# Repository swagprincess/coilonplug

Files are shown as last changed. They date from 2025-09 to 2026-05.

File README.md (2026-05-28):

# Dwell converter board

This board lets you use a Toyota/Audi/etc "coil on plug" ignition system with the stock ecu in a Mazda MX5/Miata (1989-2005).

The board will take in a variable dwell signal for the stock coilpack and output a (falling edge synchronised) stable, adjustable dwell pulse.

Current setting is 70 "ticks" of TIMER1, around 2.2ms, correct for Toyota COP's at running voltages (should be good for Audi R8 coils too).

Written in C for an AtTiny84A.

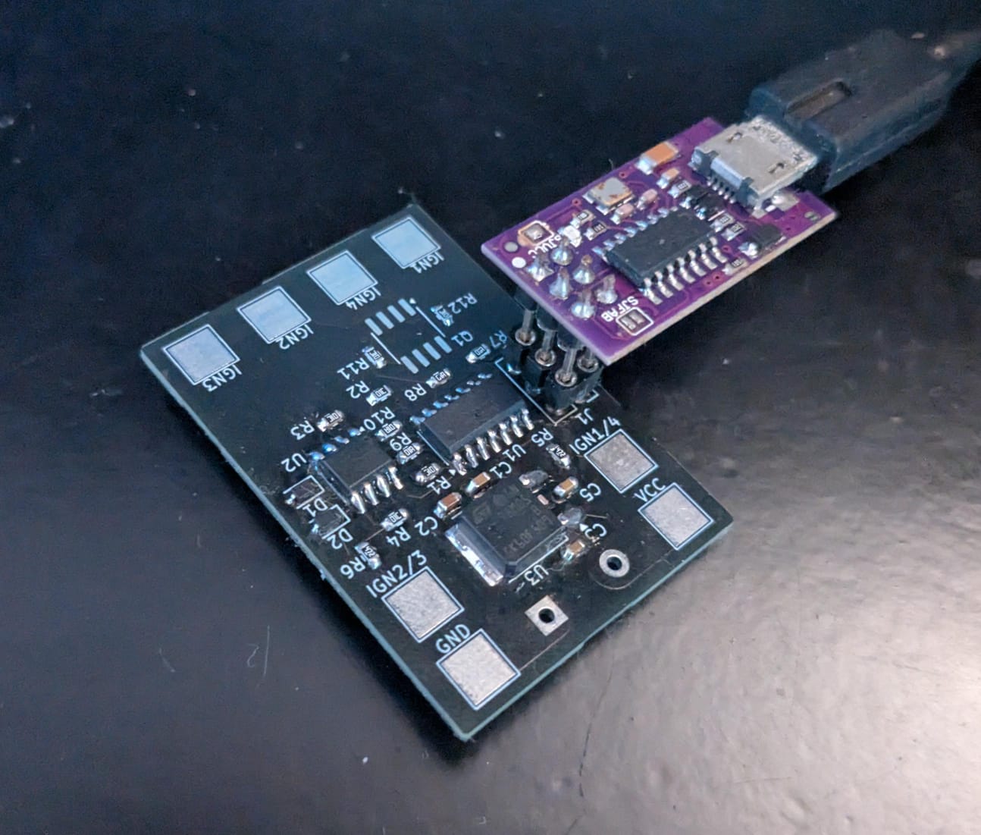
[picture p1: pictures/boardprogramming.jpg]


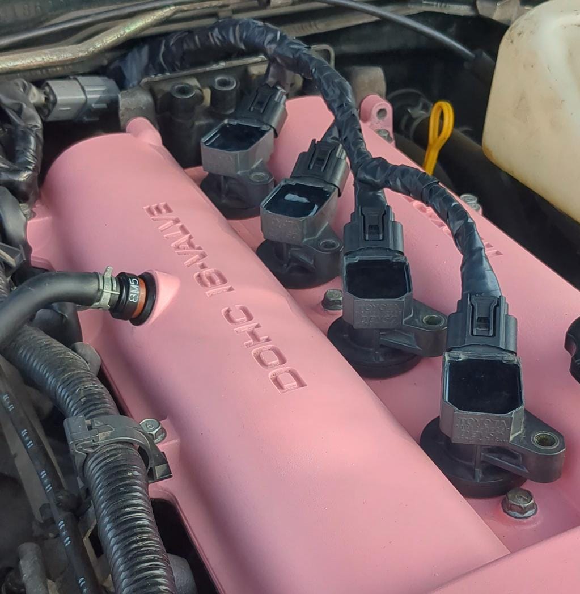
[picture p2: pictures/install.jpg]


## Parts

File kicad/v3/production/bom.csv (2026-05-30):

Designator | Footprint | Quantity | Value | LCSC Part #
C1, C3 | 0603 | 2 | 100n | C77055
C2 | 0603 | 1 | 330n | C354382
C4 | 0603 | 1 | 10u | C2959727
D1, D2 | D_SOD-323F | 2 | MM3Zxx | C154578
Q1 | SOIC-8_3.9x4.9mm_P1.27mm | 1 | DMP3098LSD-13 | C531177
R1, R2, R3, R4 | 0603 | 4 | 10k | C116677
U1 | SOIC-14_3.9x8.7mm_P1.27mm | 1 | ATtiny84A-SS | C1340034
U2, U3 | SOT-23-5 | 2 | SN74LVC1G17DBVR | C7836
U4 | SOT-89-3 | 1 | L78L05_SOT89 | C42738

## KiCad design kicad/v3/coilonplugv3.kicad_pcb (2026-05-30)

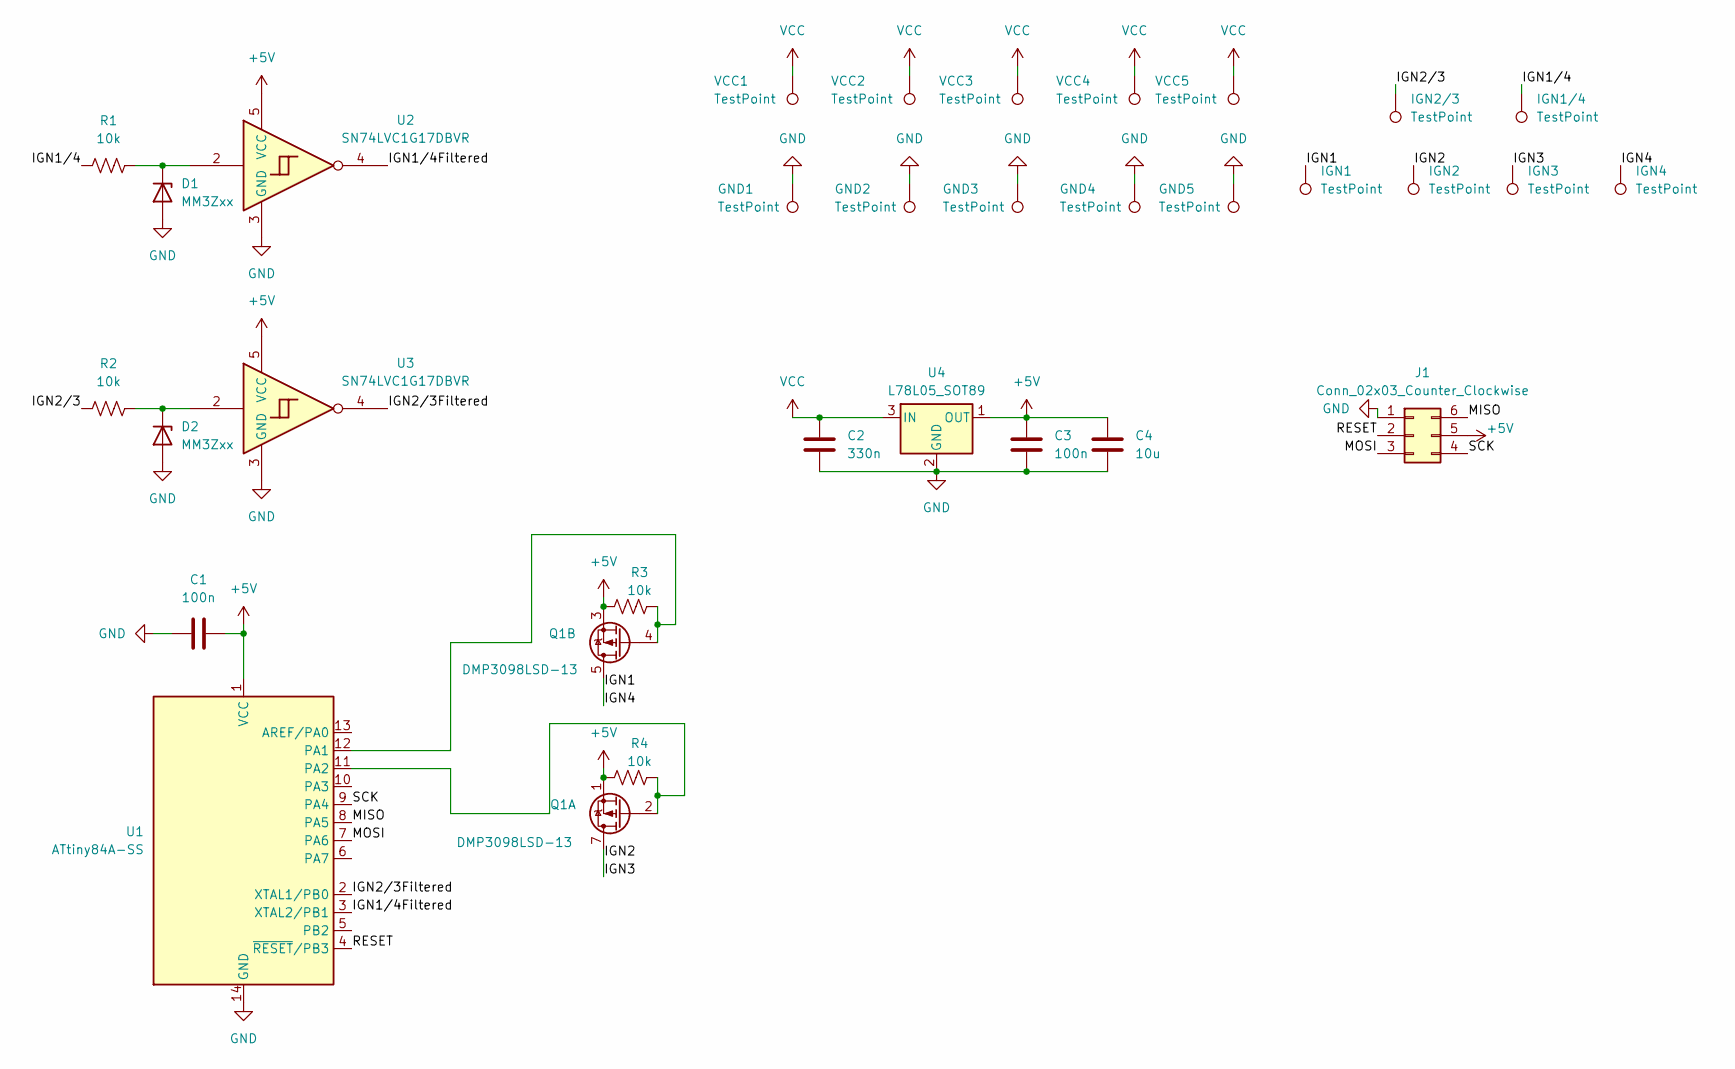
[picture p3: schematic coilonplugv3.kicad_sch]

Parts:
C1, C3: 100n; C_0603_1608Metric; LCSC Part # C77055
C2: 330n; C_0603_1608Metric; LCSC Part # C354382
C4: 10u; C_0603_1608Metric; LCSC Part # C2959727
D1, D2: MM3Zxx; D_SOD-323F; LCSC Part # C154578
GND1, GND2, GND3, GND4, GND5: TestPoint; TestPoint_Pad_2.5x2.5mm
IGN1, IGN1/4, IGN2, IGN2/3, IGN3, IGN4: TestPoint; TestPoint_Pad_2.5x2.5mm
J1: Conn_02x03_Counter_Clockwise; PinHeader_2x03_P2.54mm_Vertical; LCSC Part # C2764576
Q1: DMP3098LSD-13; SOIC-8_3.9x4.9mm_P1.27mm; LCSC Part # C531177
R1, R2, R3, R4: 10k; R_0603_1608Metric; LCSC Part # C116677
U1: ATtiny84A-SS; SOIC-14_3.9x8.7mm_P1.27mm; LCSC Part # C1340034
U2, U3: SN74LVC1G17DBVR; SOT-23-5; LCSC Part # C7836
U4: L78L05_SOT89; SOT-89-3; LCSC Part # C42738
VCC1, VCC2, VCC3, VCC4, VCC5: TestPoint; TestPoint_Pad_2.5x2.5mm

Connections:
+5V: C1.1, C3.1, C4.1, J1.5, Q1.1 (S1), Q1.3 (S2), R3.2, R4.2, U1.1 (VCC), U2.5 (VCC), U3.5 (VCC), U4.1 (OUT)
/IGN1: IGN1.1 (1_1), IGN4.1 (1_1), Q1.5 (D2), Q1.6 (D2)
/IGN1/4: IGN1/4.1 (1_1), R1.1
/IGN1/4Filtered: U1.3 (XTAL2/PB1), U2.4
/IGN2: IGN2.1 (1_1), IGN3.1 (1_1), Q1.7 (D1), Q1.8 (D1)
/IGN2/3: IGN2/3.1 (1_1), R2.1
/IGN2/3Filtered: U1.2 (XTAL1/PB0), U3.4
/MISO: J1.6, U1.8 (PA5)
/MOSI: J1.3, U1.7 (PA6)
/RESET: J1.2, U1.4 (~RESET/PB3)
/SCK: J1.4, U1.9 (PA4)
GND: C1.2, C2.2, C3.2, C4.2, D1.2 (A), D2.2 (A), GND1.1 (1_1), GND2.1 (1_1), GND3.1 (1_1), GND4.1 (1_1), GND5.1 (1_1), J1.1, U1.14 (GND), U2.3 (GND), U3.3 (GND), U4.2 (GND)
unnamed: D1.1 (K), R1.2, U2.2
unnamed: D2.1 (K), R2.2, U3.2
unnamed: Q1.2 (G1), R4.1, U1.11 (PA2)
unnamed: Q1.4 (G2), R3.1, U1.12 (PA1)
VCC: C2.1, U4.3 (IN), VCC1.1 (1_1), VCC2.1 (1_1), VCC3.1 (1_1), VCC4.1 (1_1), VCC5.1 (1_1)

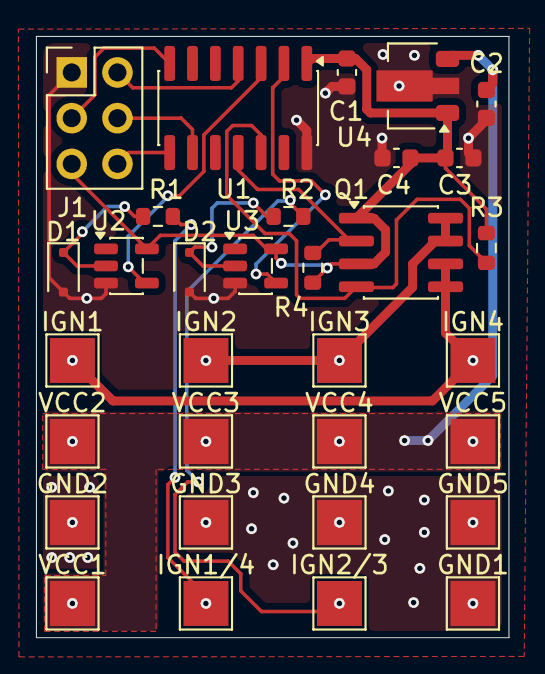
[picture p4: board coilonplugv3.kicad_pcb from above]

Board: 2 copper layers, 26.2 x 33.4 mm, 32 parts (0 on the bottom side), 17 nets.

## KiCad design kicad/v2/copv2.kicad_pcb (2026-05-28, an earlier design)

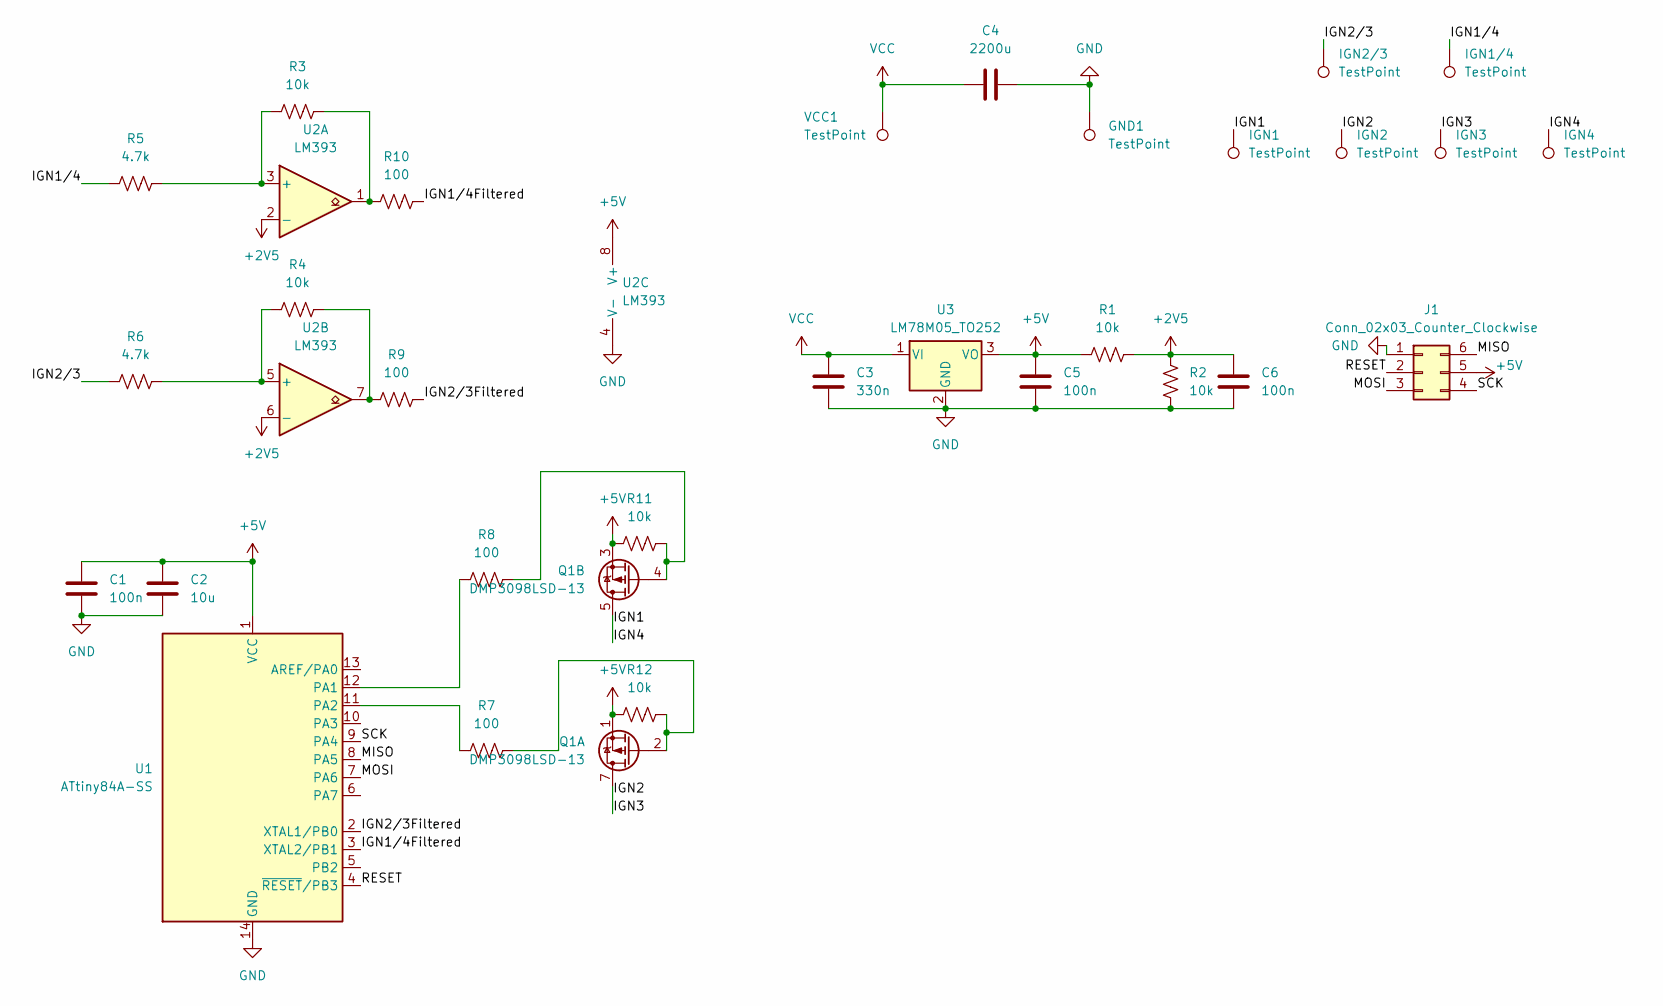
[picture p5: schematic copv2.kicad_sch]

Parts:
C1, C5, C6: 100n; C_0603_1608Metric; LCSC Part # C77055
C2: 10u; C_0603_1608Metric; LCSC Part # C2959727
C3: 330n; C_0603_1608Metric; LCSC Part # C107070
C4: 2200u; CP_Radial_D12.5mm_P5.00mm; LCSC Part # C111500
GND1: TestPoint; TestPoint_Pad_4.0x4.0mm
IGN1, IGN1/4, IGN2, IGN2/3, IGN3, IGN4: TestPoint; TestPoint_Pad_4.0x4.0mm
J1: Conn_02x03_Counter_Clockwise; PinHeader_2x03_P2.54mm_Vertical; LCSC Part # C2764576
Q1: DMP3098LSD-13; SOIC-8_3.9x4.9mm_P1.27mm; LCSC Part # C531177
R1, R2, R3, R4, R11, R12: 10k; R_0603_1608Metric; LCSC Part # C98220
R5, R6: 4.7k; R_0603_1608Metric; LCSC Part # C116697
R7, R8, R9, R10: 100; R_0603_1608Metric; LCSC Part # C105588
U1: ATtiny84A-SS; SOIC-14_3.9x8.7mm_P1.27mm; LCSC Part # C1340034
U2: LM393; SOIC-8_3.9x4.9mm_P1.27mm; LCSC Part # C32901
U3: LM78M05_TO252; TO-252-2; LCSC Part # C58069
VCC1: TestPoint; TestPoint_Pad_4.0x4.0mm

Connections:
+2V5: C6.1, R1.2, R2.2, U2.2 (-), U2.6 (-)
+5V: C1.1, C2.1, C5.1, J1.5, Q1.1 (S1), Q1.3 (S2), R1.1, R11.2, R12.2, U1.1 (VCC), U2.8 (V+), U3.3 (VO)
/IGN1: IGN1.1, IGN4.1, Q1.5 (D2), Q1.6 (D2)
/IGN1/4: IGN1/4.1, R5.1
/IGN1/4Filtered: R10.1, U1.3 (XTAL2/PB1)
/IGN2: IGN2.1, IGN3.1, Q1.7 (D1), Q1.8 (D1)
/IGN2/3: IGN2/3.1, R6.1
/IGN2/3Filtered: R9.1, U1.2 (XTAL1/PB0)
/MISO: J1.6, U1.8 (PA5)
/MOSI: J1.3, U1.7 (PA6)
/RESET: J1.2, U1.4 (~RESET/PB3)
/SCK: J1.4, U1.9 (PA4)
GND: C1.2, C2.2, C3.2, C4.1, C5.2, C6.2, GND1.1, J1.1, R2.1, U1.14 (GND), U2.4 (V-), U3.2 (GND); also elsewhere on the board
unnamed: Q1.2 (G1), R7.2, R12.1
unnamed: Q1.4 (G2), R8.1, R11.1
unnamed: R4.2, R9.2, U2.7
unnamed: R3.2, R10.2, U2.1
unnamed: R8.2, U1.12 (PA1)
unnamed: R7.1, U1.11 (PA2)
unnamed: R3.1, R5.2, U2.3 (+)
unnamed: R4.1, R6.2, U2.5 (+)
VCC: C3.1, C4.2, U3.1 (VI), VCC1.1; also elsewhere on the board

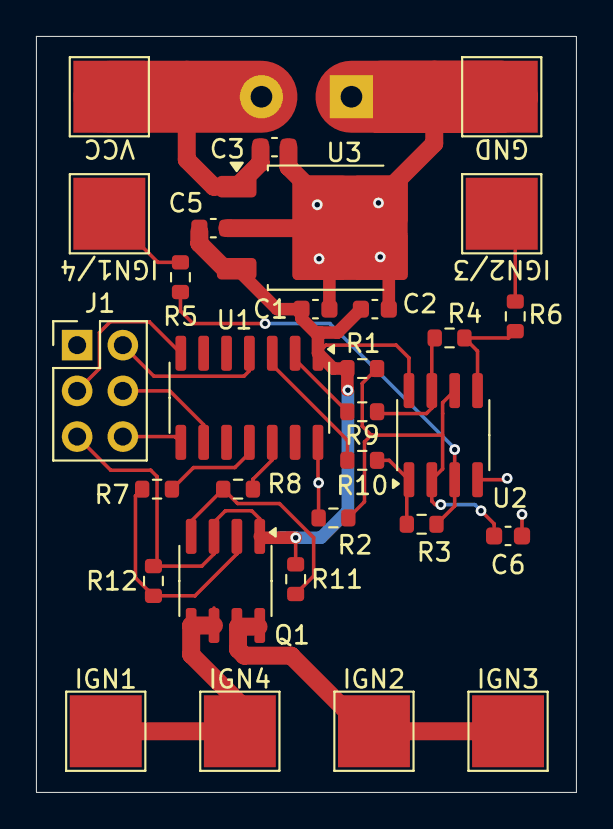
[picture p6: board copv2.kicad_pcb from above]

Board: 2 copper layers, 30.0 x 42.0 mm, 31 parts (1 on the bottom side), 22 nets.

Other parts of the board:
GND: TestPoint; TestPoint_Pad_4.0x4.0mm
VCC: TestPoint; TestPoint_Pad_4.0x4.0mm

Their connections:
GND: GND.1; also elsewhere on the board
VCC: VCC.1; also elsewhere on the board

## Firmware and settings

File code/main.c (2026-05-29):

#define F_CPU 8000000UL

#include <avr/io.h>
#include <util/delay.h>
#include <avr/interrupt.h>
#include <stdint.h>
#include <stdlib.h>

#define true 1
#define false 0

volatile uint16_t delayBeforeLow = 0;  // passthrough test //ticks at 8mhz prescaler 256, assume 5ms base pulse and 3.5ms ish for first pulse
volatile uint16_t startTime14 = 0;
volatile uint16_t startTime23 = 0;
volatile uint16_t timeToGoLow23 = 0;
volatile uint16_t timeToGoLow14 = 0;
volatile uint8_t pulses = 0;
volatile uint8_t lastState23 = false;
volatile uint8_t lastState14 = false;
volatile uint8_t set23Low = false;
volatile uint8_t set14Low = false;


ISR(PCINT1_vect){ // interrupt for all port b pins

    uint8_t pins = PINB;

    if (!(pins & (1 << PB1)) && lastState14){    //IGN 1 & 4
        // PB1 is LOW, turn off PA2 (1 & 4)
        PORTA |= (1 << PA1); // set high for off

        delayBeforeLow = (uint16_t)(TCNT1 - startTime14) - 70; //2.2ms
        if (pulses <= 30){
            delayBeforeLow = (uint16_t)(TCNT1 - startTime14) - 110; // 3.5ms for startup first 30 igniton events
            pulses = pulses + 1;
        }

        lastState14 = false;
    }

    
    if (!(pins & (1 << PB0)) && lastState23){    //IGN 2 & 3
        // PB0 is LOW, turn off PA1 (2 & 3)
        PORTA |= (1 << PA2); // set high for off

        delayBeforeLow = (uint16_t)(TCNT1 - startTime23) - 70; //2.2ms
        if (pulses <= 30){
            delayBeforeLow = (uint16_t)(TCNT1 - startTime23) - 110; // 3.5ms for startup first 30 igniton events
            pulses = pulses + 1;
        }

        lastState23 = false;
    }


    if ((pins & (1 << PB1)) && !lastState14) {   //IGN 1 & 4
        // PB1 is HIGH
        startTime14 = (uint16_t)TCNT1; // set timer timestamp

        if (delayBeforeLow < 1){
            delayBeforeLow = 0;
        }

        timeToGoLow14 = (uint16_t)(startTime14 + delayBeforeLow);

        set14Low = true; // mark pin as has to go low eventually 

        lastState14 = true;
    }

 
    if ((pins & (1 << PB0)) && !lastState23) {   //IGN 2 & 3
        // PB0 is HIGH
        startTime23 = (uint16_t)TCNT1; // set timer timestamp

        if (delayBeforeLow < 1){
            delayBeforeLow = 0;
        }

        timeToGoLow23 = (uint16_t)(startTime23 + delayBeforeLow);

        set23Low = true; // mark pin as has to go low eventually 
        
        lastState23 = true;
    }
     
}


int main(void) {

    //set output pins as output and set high
    DDRA |= ((1 << DDA1) | (1<< DDA2));
    PORTA |= ((1 << PA1) | (1 << PA2));

    //set input pins as input
    DDRB &= ~((1 << DDB0) | (1 << DDB1));

    TCCR1B = 0; // stop timer

    TCCR1B |= (1 << CS12); // start timer at prescaler 256

    GIMSK |= (1 << PCIE1); //enable group 1 pin interrupts
    PCMSK1 |= (1 << PCINT8) | (1 << PCINT9); // allow pins to trigger interrupt

    sei(); //enable interrupts


    while (1){
        if (set23Low){
            cli(); //16 bit math and time sensitive stuff
            if ((uint16_t)TCNT1 >= timeToGoLow23){
                PORTA &= ~(1 << PA2); // set low to start trigger
                set23Low = false;
            }
            sei(); //enable interrupts
        }
        if (set14Low){
            cli(); //16 bit math and time sensitive stuff 
            if ((uint16_t)TCNT1 >= timeToGoLow14){
                PORTA &= ~(1 << PA1); // set low to start trigger
                set14Low = false;
            }
            sei(); //enable interrupts
        }
    }

}

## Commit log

2025-08-10 fix bunch of bs lol
    [main.c]
2025-08-10 fix bug with negative delays
    [main.c]
2025-08-11 fix base pulse delay
    [main.c]
2025-08-11 kicad added
    [bom.csv, copv2.kicad_pcb, copv2.kicad_sch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]
2025-08-11 add cap on 2.5V
    [bom.csv, copv2.kicad_pcb, copv2.kicad_sch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]
2025-08-11 added vias around new capacitor
    [copv2.kicad_pcb]
2025-08-14 fix stuff idk
    [bom.csv, copv2.kicad_pcb, copv2.kicad_sch]
2025-08-14 move via slightly
    [copv2.kicad_pcb]
2025-09-02 mosfet wrong way around
    [copv2.kicad_pcb, copv2.kicad_sch]
2025-11-14 change output pins for new pcb revision
    [designators.csv, positions.csv]
2026-05-28 inital desgin of v3 completed
    [bom.csv, coilonplugv3.kicad_pcb, coilonplugv3.kicad_sch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]
2026-05-28 small pcb changes + get code from latest pcb made
    [bom.csv, coilonplugv3.kicad_pcb, coilonplugv3.kicad_sch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]
2026-05-29 test failed, try new code
    [coilonplugv3.kicad_pcb]
2026-05-29 found bug and fixed maybe
    [main.c]
2026-05-29 verified code working on v2 board, to be tested on v3 when ordered
2026-05-30 capacitor brand change before order
    [bom.csv, coilonplugv3.kicad_pcb, coilonplugv3.kicad_sch]
2026-05-30 ordered! state of repository when pcb ordered
    [coilonplugv3.kicad_pcb]
